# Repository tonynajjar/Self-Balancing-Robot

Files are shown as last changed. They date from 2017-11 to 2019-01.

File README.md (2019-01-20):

# Steady
Self-Balancing Robot: https://www.youtube.com/watch?time_continue=1&v=wG_vcWqeqLw

This project aimed to design, construct and program a self-balancing robot. The following objectives have been set:

* Design and assemble the chassis of the robot
* Mount all the electronic hardware on the chassis and make all the electrical connections
* Develop the software to read from the sensors and to control the actuators
* Implement a PID controller to enable the robot to stay upright
* Implement a PID controller to enable the robot to return to move
* Develop the software for wireless control and camera streaming

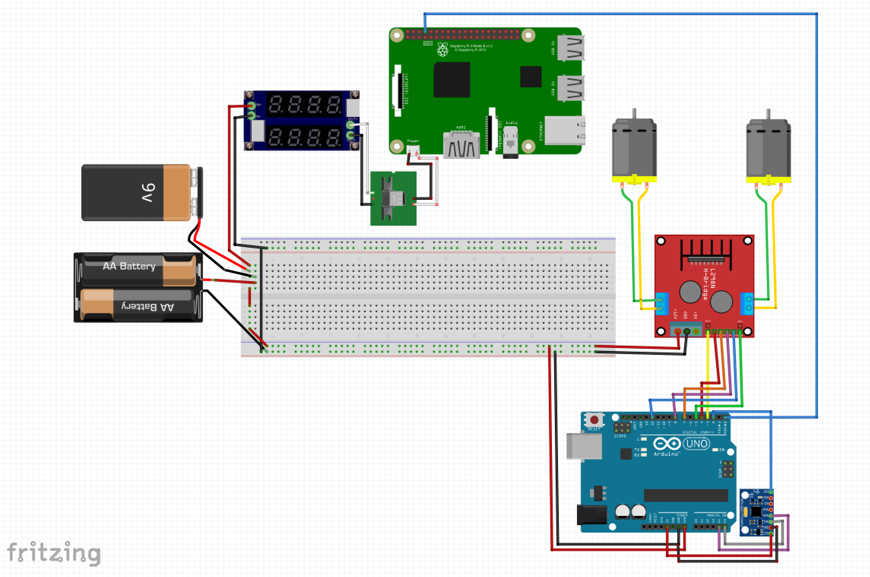
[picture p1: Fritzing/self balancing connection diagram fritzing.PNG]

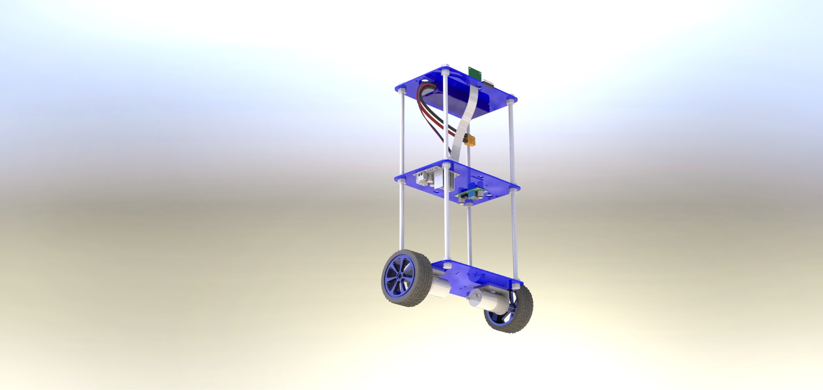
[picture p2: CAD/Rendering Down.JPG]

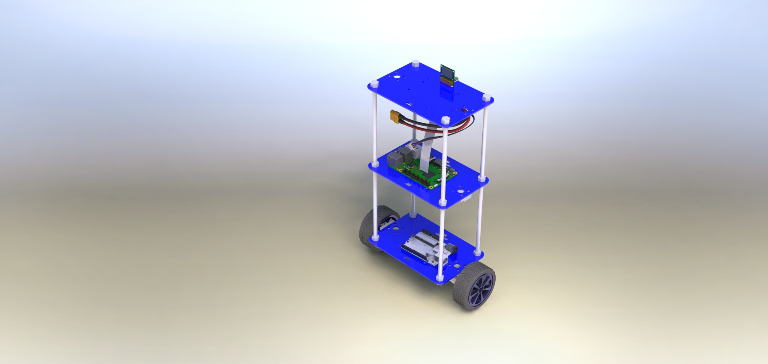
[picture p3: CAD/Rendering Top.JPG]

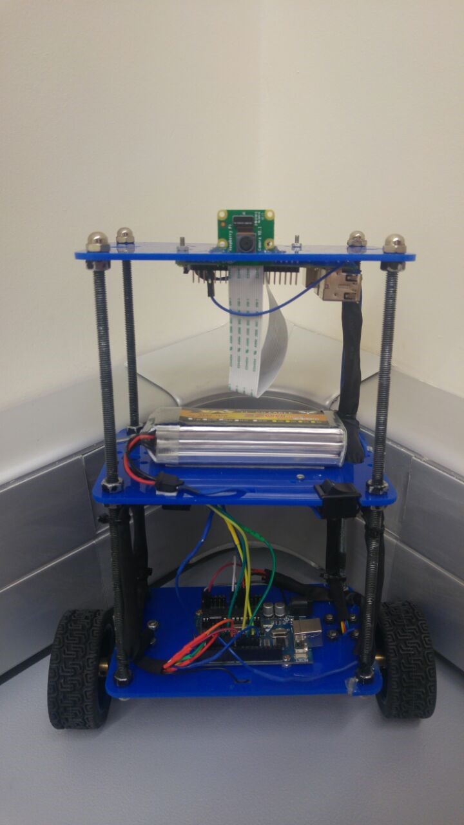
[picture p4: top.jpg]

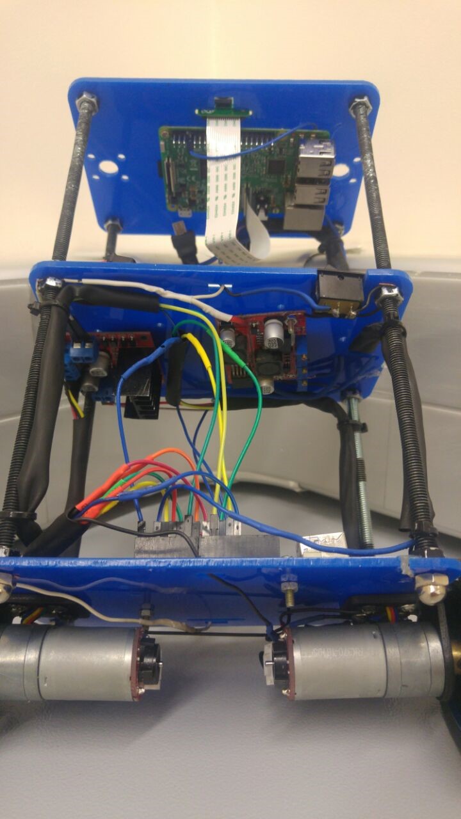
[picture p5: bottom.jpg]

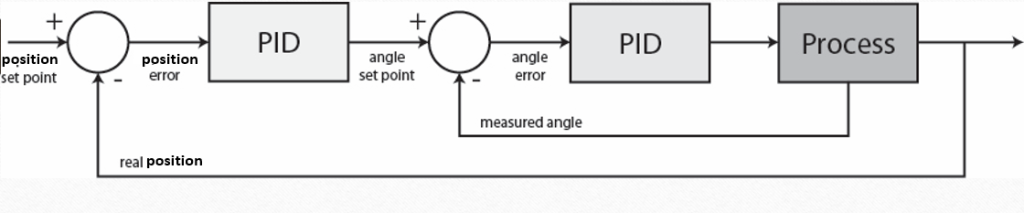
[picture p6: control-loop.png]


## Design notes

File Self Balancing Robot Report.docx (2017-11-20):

Introduction

Self-balancing robots have been a topic of interest of many researchers, students and hobbyists worldwide. In essence, it is an inverted pendulum on wheels, a derivative of the inverted pendulum on a cart. Unlike traditional robots, which are in a constant state of equilibrium, the self-balancing robot is a naturally unstable system; its design is more complex, as it needs to be actively controlled to maintain its upright position. The primary practical application of a self-balancing robot is human transportation, which was popularized by the release of the Segway.

This project aims to design, construct and program a self-balancing robot. To achieve the aims of the project, following objectives have been set:

- Design and assemble the chassis of the robot
- Mount all the electronic hardware on the chassis and make all the electrical connections
- Develop the software to read from the sensors and to control the actuators
- Implement a PID controller to enable the robot to stay upright
- Implement a PID controller to enable the robot to return to its original position if pushed
- Develop the software for wireless control and camera streaming

This report discusses the theoretical considerations made at the start of the project, the steps that were taken to implement the self-balancing code, the analysis of the final results, the interpretation of the final results and finally the recommendations for future continuation of the project

Background research

The inverted pendulum is a classical problem in control systems, and to explore the unstable dynamics, different platforms have been developed. These platforms are similar in many ways, leading to many of the behaviors being comparable. The most common types are the self-balancing robot, Inverted Pendulum on a cart and an inverted pendulum on a linear track, shown in the figure below:

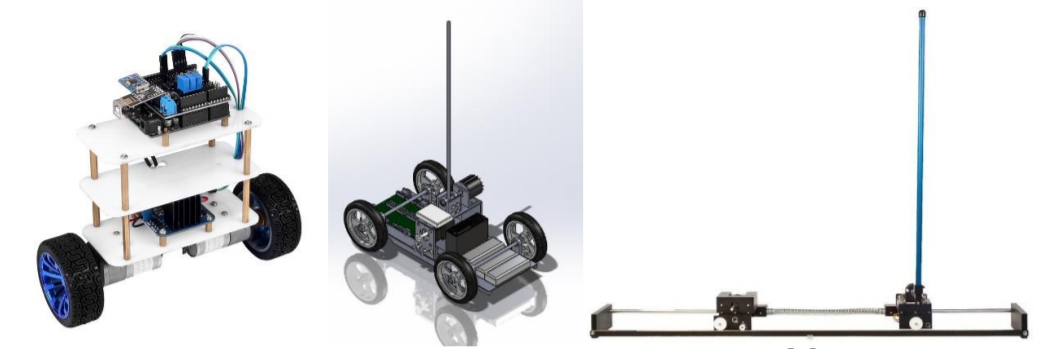
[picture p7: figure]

The Segway is a dynamic system that is commonly referred to as an inverted pendulum.

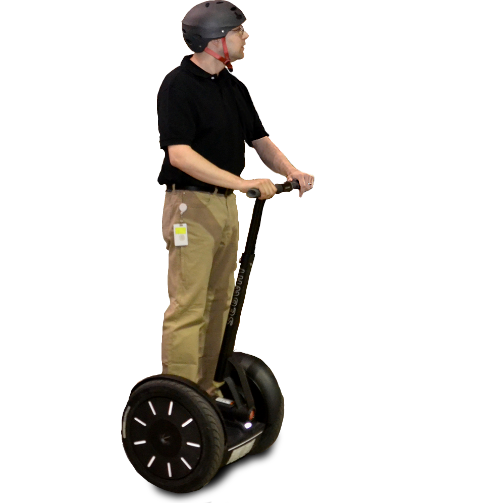
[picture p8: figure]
Image result for segway

To form a two-wheeled inverted pendulum (TWIP), the pendulum is anchored to a base platform that has a wheel mounted on each side. In this case, a motor drives each wheel independently. The torque from the motors makes the base move to balance pitch angle of the pendulum. It can move along curved paths by driving the motors at different speeds. The two-wheeled inverted pendulum has been proposed as a portable transporter due to its high maneuverability

The Segway is a device that transports one person at relatively low speeds. The low-speed (limited to approximately 12 mph) operation combined with its electric propulsion system makes the Segway a candidate for providing short-distance transportation on city streets, sidewalks, and inside buildings. When a Segway is in use, the device is driven by two wheels that are placed side-by-side, rather than the standard in-line configuration of a bicycle or a motorcycle. When the operator leans forward, the wheels turn in unison in the same direction to provide forward motion. In order to stop, the wheels must accelerate forward to get out in front of the system's center of mass and then apply a deceleration torque to slow the system down without causing the operator to fall forward of the device. These operating principles are reversed to allow the system to move backward. In order to turn, the wheels rotate at unequal speeds causing the system to travel in an arc. If the system is not translating forward or backward, then the wheels can rotate in opposite directions to turn the machine in place. Given the side-by-side wheel configuration, and the elevated center of mass, the mechanical design of the transporter is unstable. It will fall over if the computerized control system is not continuously turning the wheels. This constant adjusting of the device is similar to a person balancing an inverted broom in their hand. In order to keep the broom upright, the person must continually move their hand in the direction that the broom is falling. The broom's center of mass to generate a torque that will cause the broom to start rotating in the opposite direction. As a result, the broom is always falling, but the hand motion keeps changing the direction of the fall. Just like the inverted broom, the Segway and rider are always falling. However, it is not possible for the human operator to balance the device, as they can with a human-powered inverted pendulum such as a unicycle. The sensors in the device must constantly be measuring the state of the machine and feeding this information to the computer controller. The controller then uses this feedback signal to adjust the wheel speed so that the forward/backward (pitch) falling motion is maintained within an acceptable envelope so that device and rider do not fall over. Note that under many operating conditions, the system is mechanically stable in the side-to-side (roll) direction. Therefore, the computer does not attempt to control the roll motion. Assuming wheel-ground rolling stiction, the system is also stable in the yaw direction. However, the computer must change the yaw rate in order to turn the machine in 10 response to the operator input. It also limits the turning rate to a maximum value

Technical discussion / simulation study

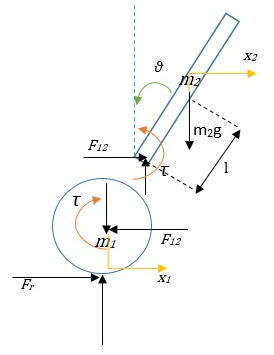
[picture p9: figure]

The control algorithm that is used to maintain the balance on the autonomous self-balancing robot is the PID controller. The proportional, integral, and derivative (PID) controller is well known as a three term controller. The input to the controller is the error from the system. The Kp, Ki, and Kd are referred as the proportional, integral, and derivative constants (the three terms get multiplied by these constants) respectively. In the PID controller the error gets managed in three ways. The error will be used on the PID controller to execute the proportional term, integral term for reduction of steady state errors, and the derivative term to handle overshoots

Results

Conclusion

During the project a robot has been designed and built from scratch. Mechanically it looks and works as planned. A mathematical model of the robot and two control designs were calculated and simulated to verify the systems behavior.

References

Appendix

http://oaktrust.library.tamu.edu/bitstream/handle/1969.1/155306/SUNG-THESIS-2015.pdf?sequence=1

http://publications.lib.chalmers.se/records/fulltext/163397.pdf

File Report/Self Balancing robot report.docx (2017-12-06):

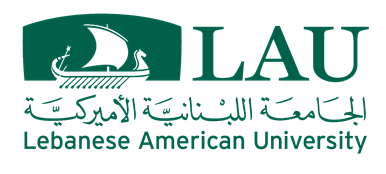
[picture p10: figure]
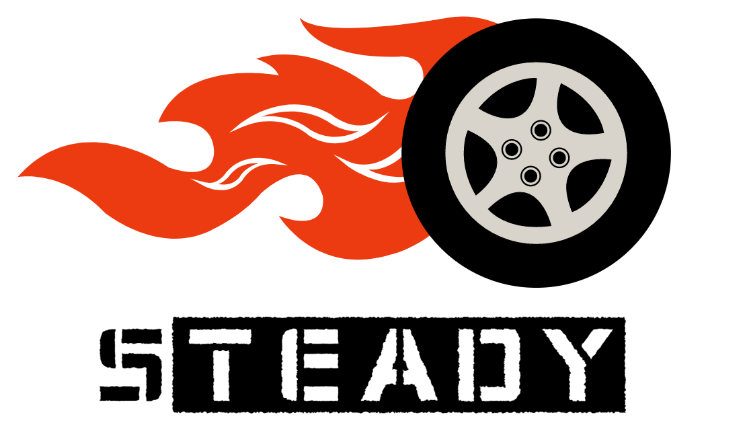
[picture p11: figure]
A picture containing vector graphics Description generated with high confidence

# Self-Balancing

# Robot

Tony Najjar

Walid Aboul hosn

# Introduction

Self-balancing robots have been a topic of interest of many researchers, students and hobbyists worldwide. It is essentially an inverted pendulum on wheels, a derivative of the inverted pendulum on a cart. Unlike traditional robots, which are in a constant state of equilibrium, the self-balancing robot is a naturally unstable system; its design is more complex, as it needs to be actively controlled to maintain its upright position. The primary practical application of a self-balancing robot is human transportation, which was popularized by the release of the Segway.

- This project aims to design, construct and program a self-balancing robot. To achieve the aims of the project, following objectives have been set:
- Design and assemble the chassis of the robot
- Mount all the electronic hardware on the chassis and make all the electrical connections
- Develop the software to read from the sensors and to control the actuators
- Implement a PID controller to enable the robot to stay upright
- Implement a PID controller to enable the robot to return to move
- Develop the software for wireless control and camera streaming

A self-balancing robot has been designed and built from scratch. Mechanically it looks and works as planned. A mathematical model of the robot and a PID control architecture were calculated and simulated to verify the system’s behavior. The PID controllers were successfully implemented on the robot together with a Kalman filter to make it balance, even with disturbances.

# Background Research

The inverted pendulum is a classical problem in control systems, and to explore the unstable dynamics, different platforms have been developed. These platforms are similar in many ways, leading to many of the behaviors being comparable. The most common types are the self-balancing robot, Inverted Pendulum on a cart and an inverted pendulum on a linear track, shown in the figure below:


The most renowned practical application of the inverted pendulum is the Segway, a dynamic system used for individual transportation.

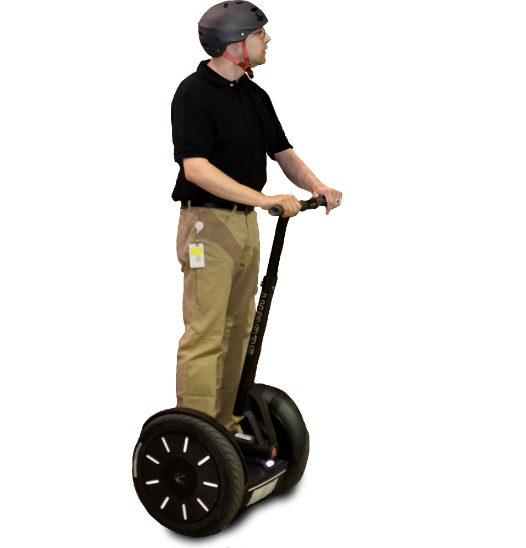
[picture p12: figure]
Image result for segway

The Segway is anchored to a base platform that has a wheel mounted on each side. In this case, a motor drives each wheel independently. The torque from the motors makes the base move to balance pitch angle of the pendulum. It can move along curved paths by driving the motors at different speeds. The two-wheeled inverted pendulum has been proposed as a portable transporter due to its high maneuverability

The Segway is a device that transports one person at relatively low speeds. The low-speed (limited to approximately 12 mph) operation combined with its electric propulsion system makes the Segway a candidate for providing short-distance transportation on city streets, sidewalks, and inside buildings. When a Segway is in use, the device is driven by two wheels that are placed side-by-side, rather than the standard in-line configuration of a bicycle or a motorcycle. When the operator leans forward, the wheels turn in unison in the same direction to provide forward motion. In order to stop, the wheels must accelerate forward to get out in front of the system's center of mass and then apply a deceleration torque to slow the system down without causing the operator to fall forward of the device. These operating principles are reversed to allow the system to move backward. In order to turn, the wheels rotate at unequal speeds causing the system to travel in an arc. If the system is not translating forward or backward, then the wheels can rotate in opposite directions to turn the machine in place. Given the side-by-side wheel configuration, and the elevated center of mass, the mechanical design of the transporter is unstable. It will fall over if the computerized control system is not continuously turning the wheels. This constant adjusting of the device is similar to a person balancing an inverted broom in their hand. In order to keep the broom upright, the person must continually move their hand in the direction that the broom is falling. The broom's center of mass to generate a torque that will cause the broom to start rotating in the opposite direction. As a result, the broom is always falling, but the hand motion keeps changing the direction of the fall. Just like the inverted broom, the Segway and rider are always falling. However, it is not possible for the human operator to balance the device, as they can with a human-powered inverted pendulum such as a unicycle. The sensors in the device must constantly be measuring the state of the machine and feeding this information to the computer controller. The controller then uses this feedback signal to adjust the wheel speed so that the forward/backward (pitch) falling motion is maintained within an acceptable envelope so that device and rider do not fall over. Note that under many operating conditions, the system is mechanically stable in the side-to-side (roll) direction. Therefore, the computer does not attempt to control the roll motion. Assuming wheel-ground rolling stiction, the system is also stable in the yaw direction.

# Technical discussion & Simulation study

## Mathematical Modeling

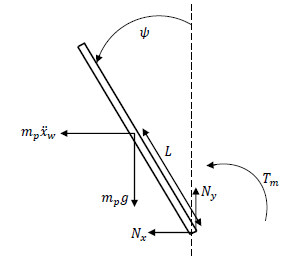
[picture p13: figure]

Pendulum

(1) Tm + mpgLsinψ + mp x wLcosψ = Jpψ
(2) −Nx − mp x w = mp x p
(3) Ny − mpg = mp y p
(4) xp = −Lsinψ
(5) yp = −Lcosψ
(6) x p = −L ψ cosψ + L ψ ² sinψ
(7) y p = −L ψ sinψ + L ψ ² cosψ

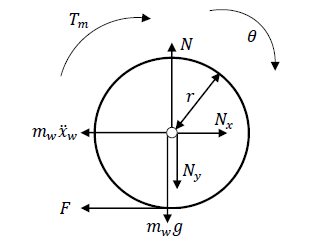
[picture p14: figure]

Wheels

(8) Tm + Fr = Jw θ
(9) Nx − mw x w − F = 0
(10) N − Ny − mwg = mw y w
(11) x w = θ r
(12) y w = 0

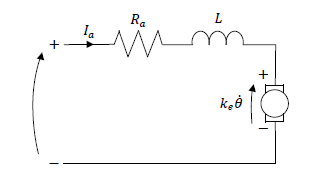
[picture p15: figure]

Motors

(13) U = RaIa + keθ
(14) Tm = nktIa
(15) Ia = U − ke θ Ra
(16) Tm = nktU Ra − nkekt θ Ra

Nonlinear Result

(17) ψ =
(18) ((Jw(gLRampsinψ + 2nkt(U – ke θ)) + r(LrRampsinψ(mp(g – Lψ2cosψ) + gmw)+2nkt(U – keθ)(mp(Lcosψ + r) + rmw))))/((Ra(Jp(Jw + r 2 (mp + mw)) – L2 r2 m2 p cos2ψ)))
(19) θ = Lrmpcosψ (gLRampsinψ + 2nkt (U − ke θ )) + Jp (2nkt (U − ke θ ) − LrRamp ψ ² sinψ (Ra (Jp (Jw + r ² (mp + mw)) − L²r ²m² p cos²ψ))

Linear Result

We can linearize the system by approximating cosθ= 1 and sinθ= θ since θ is considered very small

(20) ψ = ((Jw (gLRampψ +2nkt (U-ke θ))+r(LrRampψ (mp(g - Lψ2)+gmw)+2nkt (U-keθ)(mp (L+r) + rmw))))/((Ra(Jp(Jw + r2 (mp + mw)) - L2r2m2 p)))
(21) θ = Lrmp (gLRampψ + 2nkt (U − ke θ )) + Jp (2nkt (U − ke θ ) − LrRamp ψ ²ψ (Ra (Jp (Jw + r²(mp + mw)) − L²r ²m² p))

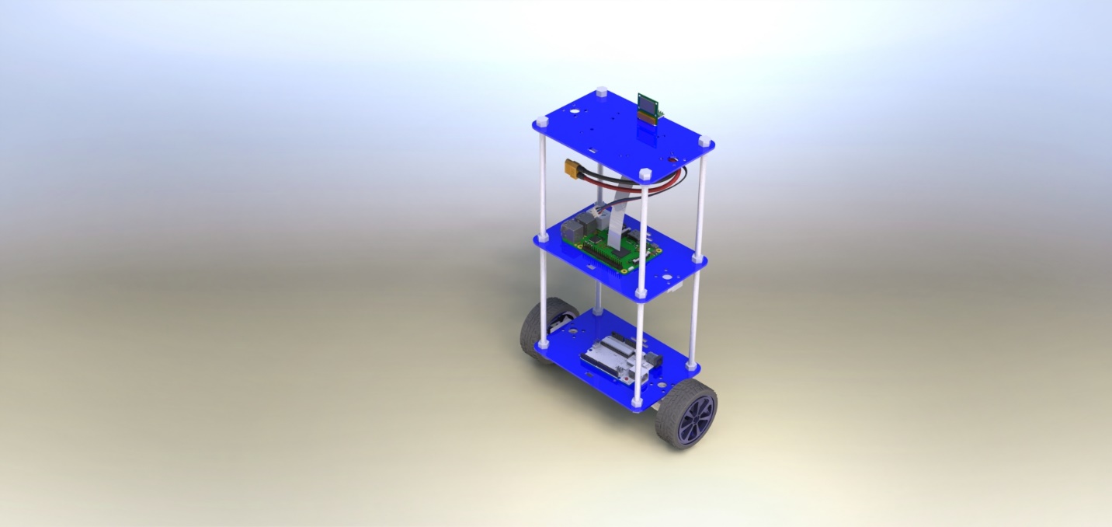
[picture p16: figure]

## CAD Modeling

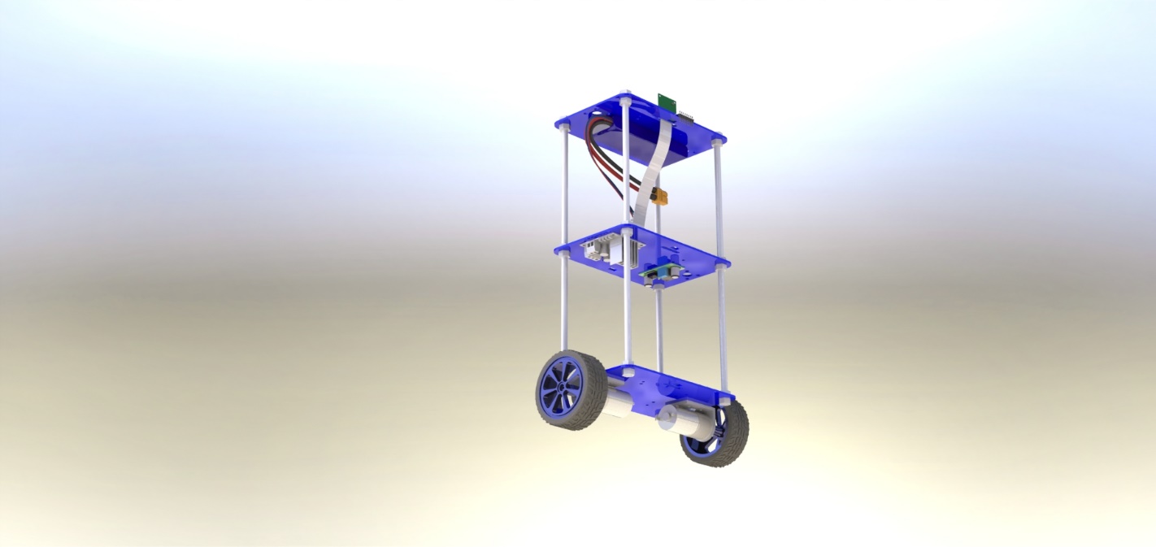
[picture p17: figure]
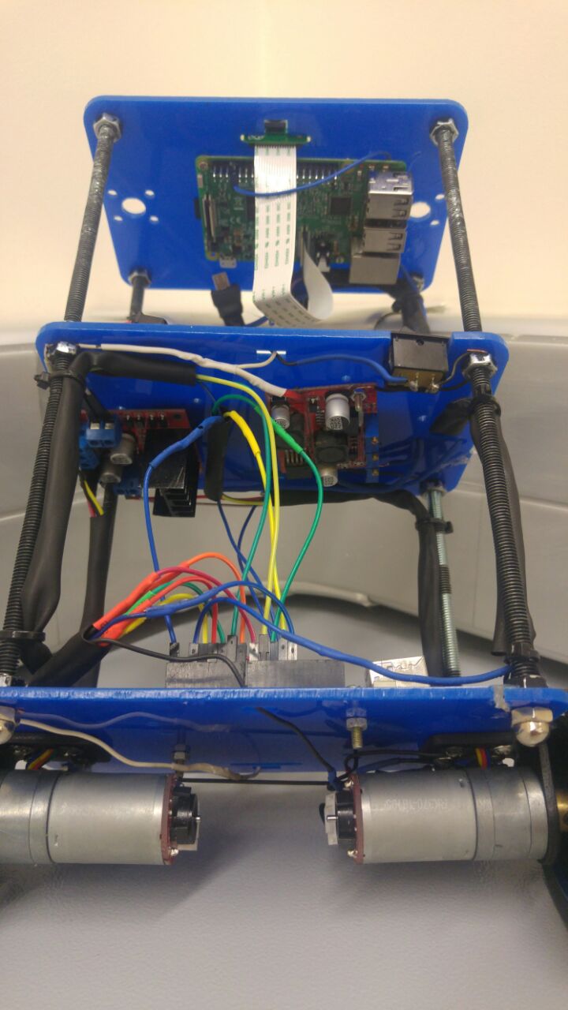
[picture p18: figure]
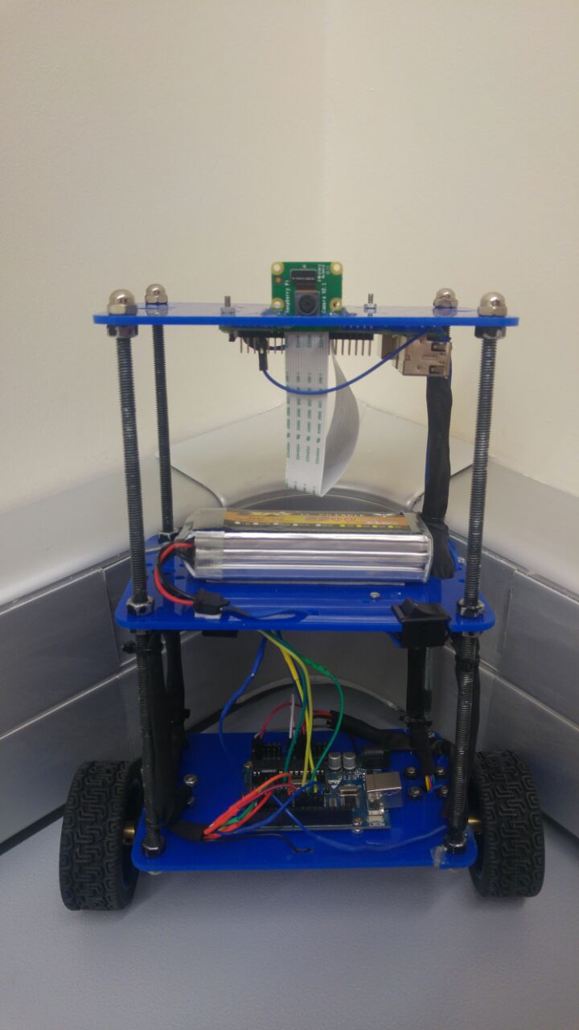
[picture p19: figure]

| Item | Quantity
Mechanical | Threaded Rods | 4
| Plexiglass Board | 3
| Motor Brackets | 2
Electrical | Arduino | 1
| Raspberry Pi | 1
| Raspberry Pi camera | 1
| IMU MPU6050 | 1
| Motor Driver L298N | 1
| Step-down DC Transformer | 1
| Battery | 1
| Geared Motors with Encoders | 2

## Hardware Wiring

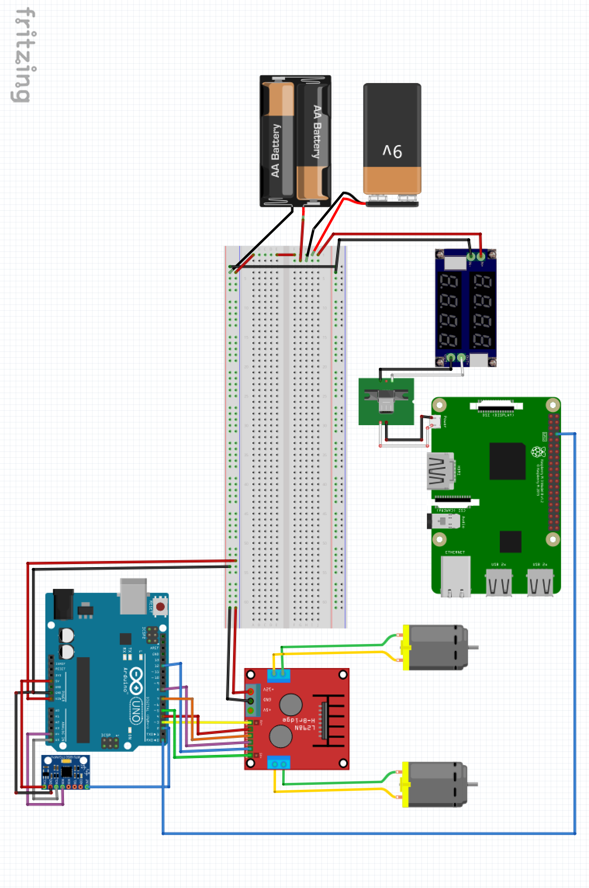
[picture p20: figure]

# Results

## Balancing Control

The control algorithm that is used to maintain the balance on the autonomous self-balancing robot is the PID controller. The proportional, integral, and derivative (PID) controller is well known as a three-term controller. The input to the controller is the error from the system. The Kp, Ki, and Kd are referred as the proportional, integral, and derivative constants (the three terms get multiplied by these constants) respectively. In the PID controller the error gets managed in three ways. The error will be used on the PID controller to execute the proportional term, integral term for reduction of steady state errors, and the derivative term to handle overshoots

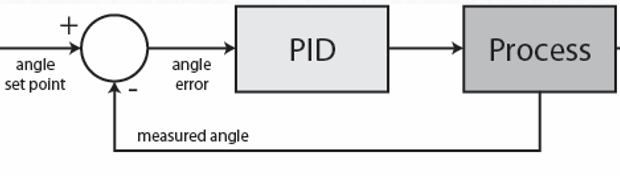
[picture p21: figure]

It is worthwhile mentioning that the LQR controller is also vastly used in inverted pendulum applications. LQR is a form of optimal control that aims to minimize the performance index whist taking into account the control effort, as often, higher input effort would imply higher energy consumption. LQR control requires derivation of the state-space model of the system, thus it is more challenging to implement.

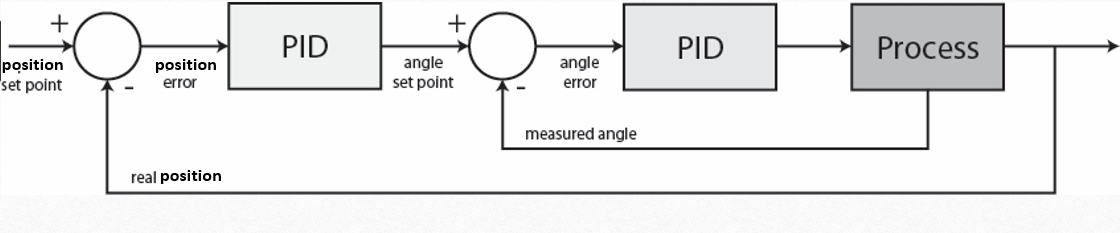
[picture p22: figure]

## Position Control

One issue with the balancing control loop is that the robot has no insight on its position and could stay upright while constantly moving. This is usually undesirable due to space constraints. To solve this issue we used parallel compensation; an extra encoder PID controller was added to the scheme to control the robot’s position. The encoder PID measures the error in position and outputs the setpoint for the angle PID loop which in turn will control the PWM of the motors. So if there's an offset in position the angle setpoint will change to, let say -2 degrees (from upright 0 degrees). So now the angle PID will make the robot move in order to correct the angle offset and therefore also correcting the position error.

## Wireless Control and Camera Streaming

Wireless control and camera streaming was implemented on the robot using a Raspberry Pi.

The small computer receives keyboard commands via Wifi and communicates them serially to the Arduino. The only factor we control is the position setpoint; we set it to be slightly positive or negative to make the robot lean forward or backward and consequently accelerate.

As for the on-board camera, the robot has the ability to wirelessly stream with minimum lag the camera’s output over the network.

# Conclusion

Overall, this self-balancing robot project was a big success, meeting all the objectives set at the beginning. The robot’s performance compares very well with other self-balancing robots found on the internet in terms of smooth balancing and position control.

We look forward to enhancing the robot in many ways such as smoothening the controllers for better transient response and adding: computer vision (to follow a ball for example), ultrasonic sensors for table/stair edge detection and side arms for fall cushioning and automatic stand up.

# References

https://www.coursehero.com/file/p1e3kuv/Other-studies-considered-changing-the-relative-position-of-the-global-center-of/

http://ieeexplore.ieee.org/iel7/6550152/6564841/06565146.pdf

http://www.ijcert.org/V2I1249.pdf

# Appendix

## Arduino

#include <PID_v1.h>

#include <LMotorController.h>

#include "I2Cdev.h"

#include <SoftwareSerial.h>

#include <Encoder.h>

#include "MPU6050_6Axis_MotionApps20.h"

#if I2CDEV_IMPLEMENTATION == I2CDEV_ARDUINO_WIRE

#include "Wire.h"

#endif

#define MOVE_BACK_FORTH 0

#define MIN_ABS_SPEED 80

Encoder left(9, 6);

Encoder right(10, 11);

long oldPosition = -999;

int encCount = 0;

//MPU

unsigned long counter;

MPU6050 mpu;

// MPU control/status vars

bool dmpReady = false; // set true if DMP init was successful

uint8_t mpuIntStatus; // holds actual interrupt status byte from MPU

uint8_t devStatus; // return status after each device operation (0 = success, !0 = error)

uint16_t packetSize; // expected DMP packet size (default is 42 bytes)

uint16_t fifoCount; // count of all bytes currently in FIFO

uint8_t fifoBuffer[64]; // FIFO storage buffer

// orientation/motion vars

Quaternion q; // [w, x, y, z] quaternion container

VectorFloat gravity; // [x, y, z] gravity vector

float ypr[3]; // [yaw, pitch, roll] yaw/pitch/roll container and gravity vector

//PID

double originalSetpoint = 174.29;

double setpoint = originalSetpoint;

double movingAngleOffset = 1.5;

double input = originalSetpoint, output;

int moveState = 0; //0 = balance; 1 = back; 2 = forth

double posInput, posOutput, posSetpoint = 0;

PID pid(&input, &output, &setpoint, 25, 240, 2, DIRECT);

PID posPID(&posInput, &posOutput, &posSetpoint, 0.8, 0, 1, REVERSE);

//MOTOR CONTROLLER

int motorSpeed;

double motorSpeedFactorLeft = 0.8;

double motorSpeedFactorRight = 1;

//MOTOR CONTROLLER

const int ENA = 3;

const int IN1 = 4;

const int IN2 = 7;

const int IN3 = 8;

const int IN4 = 12;

const int ENB = 5;

LMotorController motorController(ENA, IN1, IN2, ENB, IN3, IN4, motorSpeedFactorLeft, motorSpeedFactorRight);

//timers

long time5Hz = 0;

volatile bool mpuInterrupt = false; // indicates whether MPU interrupt pin has gone high

void dmpDataReady()

{

mpuInterrupt = true;

}

void setup()

{

// join I2C bus (I2Cdev library doesn't do this automatically)

#if I2CDEV_IMPLEMENTATION == I2CDEV_ARDUINO_WIRE

Wire.begin();

TWBR = 24; // 400kHz I2C clock (200kHz if CPU is 8MHz)

#elif I2CDEV_IMPLEMENTATION == I2CDEV_BUILTIN_FASTWIRE

Fastwire::setup(400, true);

#endif

Serial.begin(115200);

while (!Serial); // wait for Leonardo enumeration, others continue immediately

// initialize device

Serial.println(F("Initializing I2C devices..."));

mpu.initialize();

// verify connection

Serial.println(F("Testing device connections..."));

Serial.println(mpu.testConnection() ? F("MPU6050 connection successful") : F("MPU6050 connection failed"));

// load and configure the DMP

Serial.println(F("Initializing DMP..."));

devStatus = mpu.dmpInitialize();

// supply your own gyro offsets here, scaled for min sensitivity

mpu.setXGyroOffset(220);

mpu.setYGyroOffset(76);

mpu.setZGyroOffset(-85);

mpu.setZAccelOffset(1788); // 1688 factory default for my test chip

// make sure it worked (returns 0 if so)

if (devStatus == 0)

{

// turn on the DMP, now that it's ready

Serial.println(F("Enabling DMP..."));

mpu.setDMPEnabled(true);

// enable Arduino interrupt detection

Serial.println(F("Enabling interrupt detection (Arduino external interrupt 0)..."));

attachInterrupt(0, dmpDataReady, RISING);

mpuIntStatus = mpu.getIntStatus();

Serial.println(F("DMP ready! Waiting for first interrupt..."));

dmpReady = true;

// get expected DMP packet size for later comparison

packetSize = mpu.dmpGetFIFOPacketSize();

//setup PID

pid.SetMode(AUTOMATIC);

pid.SetSampleTime(100);

pid.SetOutputLimits(-255, 255);

posPID.SetMode(AUTOMATIC);

posPID.SetSampleTime(100);

posPID.SetOutputLimits(-movingAngleOffset, movingAngleOffset);

}

else{

Serial.print(F("DMP Initialization failed (code "));

Serial.print(devStatus);

Serial.println(F(")"));

}

}

void loop()

{

// if programming failed, don't try to do anything

if (!dmpReady) {

return;

}

// wait for MPU interrupt or extra packet(s) available

while (!mpuInterrupt && fifoCount < packetSize){

//Serial.println(abs(input - originalSetpoint));

if (abs(input - originalSetpoint) > 20) {

motorController.move(0);

break;

}

double newPosition = (right.read() + left.read()) / 2;

if (newPosition != oldPosition && abs(newPosition - oldPosition) > 5) {

oldPosition = newPosition;

posInput = newPosition / 100;

//Serial.println(posInput);

}

// Serial.println(posInput);

//no mpu data - performing PID calculations and output to motors

posPID.Compute();

calculateSetpoint();

pid.Compute();

if (input > setpoint + 0.3 || input < setpoint - 0.3) {

motorController.move(output, MIN_ABS_SPEED);

}

else {

motorController.move(0);

}

unsigned long currentMillis = millis();

if (currentMillis - time5Hz >= 5000)

{

//moveBackForth();

time5Hz = currentMillis;

}

}

// reset interrupt flag and get INT_STATUS byte

mpuInterrupt = false;

mpuIntStatus = mpu.getIntStatus();

// get current FIFO count

fifoCount = mpu.getFIFOCount();

// check for overflow (this should never happen unless our code is too inefficient)

if ((mpuIntStatus & 0x11) || fifoCount == 1024)

{

// reset so we can continue cleanly

mpu.resetFIFO();

Serial.println(F("FIFO overflow!"));

// otherwise, check for DMP data ready interrupt (this should happen frequently)

}

else if (mpuIntStatus & 0x02)

{

// wait for correct available data length, should be a VERY short wait

while (fifoCount < packetSize) fifoCount = mpu.getFIFOCount();

// read a packet from FIFO

mpu.getFIFOBytes(fifoBuffer, packetSize);

// track FIFO count here in case there is > 1 packet available

// (this lets us immediately read more without waiting for an interrupt)

fifoCount -= packetSize;

mpu.dmpGetQuaternion(&q, fifoBuffer);

mpu.dmpGetGravity(&gravity, &q);

mpu.dmpGetYawPitchRoll(ypr, &q, &gravity);

input = ypr[2] * 180 / M_PI + 180;

}

}

void calculateSetpoint() {

if (Serial.available()) {

counter = millis();

char c = Serial.read();

//Serial.println(c);

switch (c) {

case 'w':

motorController.setMotorConst(1, 1);

setpoint = originalSetpoint + movingAngleOffset;

break;

case 's':

motorController.setMotorConst(1, 1);

setpoint = originalSetpoint - movingAngleOffset;

break;

case 'a':

motorController.setMotorConst(0.5, 1);

setpoint = originalSetpoint + movingAngleOffset;

break;

case 'd':

motorController.setMotorConst(1, 0.5);

setpoint = originalSetpoint + movingAngleOffset;

break;

}

}

else if (millis() - counter > 500) {

posInput=0;

left.write(0);

right.write(0);

posPID.Compute();

setpoint = originalSetpoint + posOutput;

motorController.setMotorConst(0.75, 1);

}

}

## Raspberry Pi

import sys, tty, termios

import serial

ser = serial.Serial(port='/dev/serial0', baudrate=115200,

parity=serial.PARITY_NONE,

stopbits=serial.STOPBITS_ONE,

bytesize=serial.EIGHTBITS,

timeout=1)

def getch():

fd = sys.stdin.fileno()

old_settings = termios.tcgetattr(fd)

try:

tty.setraw(sys.stdin.fileno())

ch = sys.stdin.read(1)

finally:

termios.tcsetattr(fd, termios.TCSADRAIN, old_settings)

return ch

while True:

char = getch()

print char

if char == 'p':

break

ser.write(char)

## MATLAB

%Uncomment one set of PID tunings at a time and run the code

clear

M = 0.5;

m = 0.2;

b = 0.1;

I = 0.006;

g = 9.8;

l = 0.3;

q = (M+m)*(I+m*l^2)-(m*l)^2;

s = tf('s');

P_pend = (m*l*s/q)/(s^3 + (b*(I + m*l^2))*s^2/q - ((M + m)*m*g*l)*s/q - b*m*g*l/q);

%Unstable

% Kp = 10;

% Ki = 0;

% Kd = 0;

%Underdamped

Kp = 100;

Ki = 1;

Kd = 1;

%Overdamped

% Kp = 100;

% Ki = 1;

% Kd = 20;

%axis([0, 2.5, -0.2, 0.2]);

C = pid(Kp,Ki,Kd);

T = feedback(series(P_pend,C),1);

t=0:0.01:10;

[Y, T]=impulse(T,t);

h=figure;

subplot(2,1,1)

plot(T,Y)

subplot(2,1,2)

axis([-1 1 0 1.5])

for i=1:1:size(Y)

if ~ishghandle(h)

break

end

x= cosd(Y(i,1));

y= sind(Y(i,1));

link=line([0 y], [0 x], 'LineWidth' , 4);

pause(0.01);

delete(link)

end

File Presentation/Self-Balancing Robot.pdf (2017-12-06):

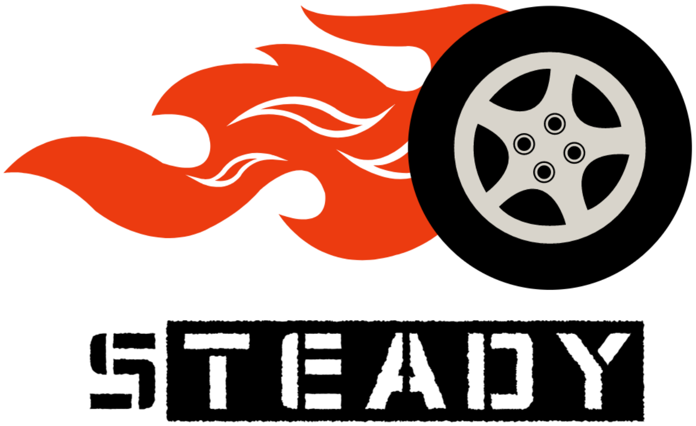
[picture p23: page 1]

# Outline

- Introduction
- Goals
- Background Research
- Working Principle
- Technical Discussion
- CAD
- Wiring and Powering
- Modeling & Simulation
- Control System
- Kalman Filter
- Future Enhancements

# Introduction

A self-balancing robot is essentially an inverted pendulum on wheels

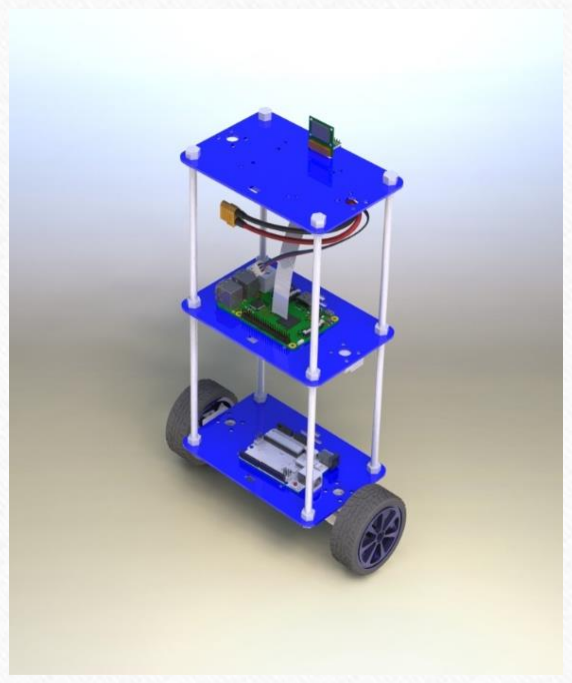
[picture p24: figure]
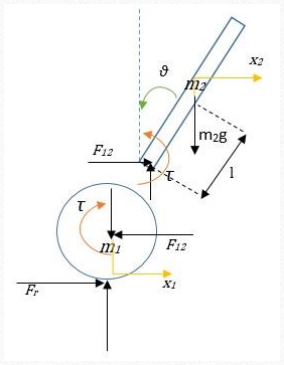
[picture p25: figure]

# Goals

To design, construct and program a self-balancing robot, the following objectives have been set:

- Design and assemble the chassis of the robot
- Mount all the electronic hardware on the chassis and make all the electrical connections
- Develop the software to read from the sensors and to control the actuators
- Implement a PID controller to enable the robot to stay upright
- Add a cascaded PID controller to control robot’s position
- Develop the software for wireless control and camera streaming

# Background Research

The most common types of inverted pendulums are the self-balancing robot, inverted pendulum on a cart and an inverted pendulum on a linear track

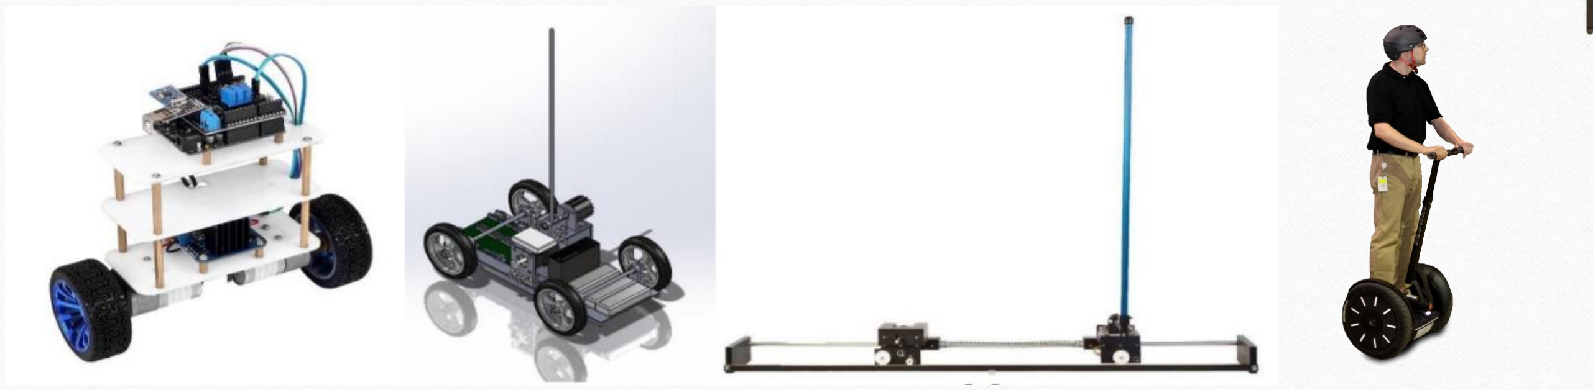
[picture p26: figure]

# Working Principle

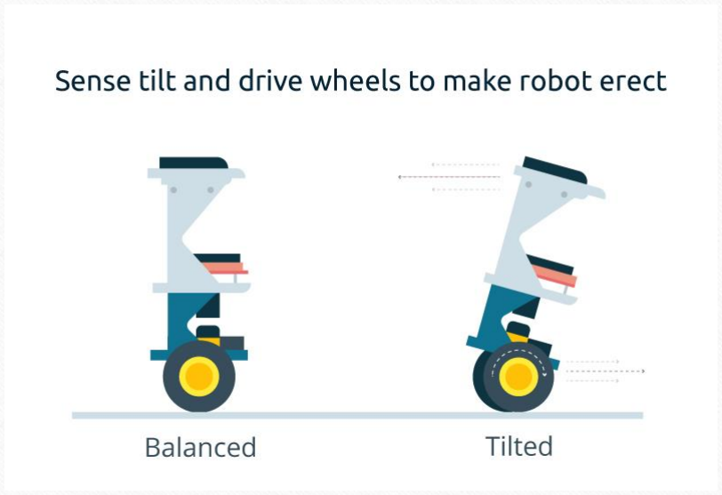
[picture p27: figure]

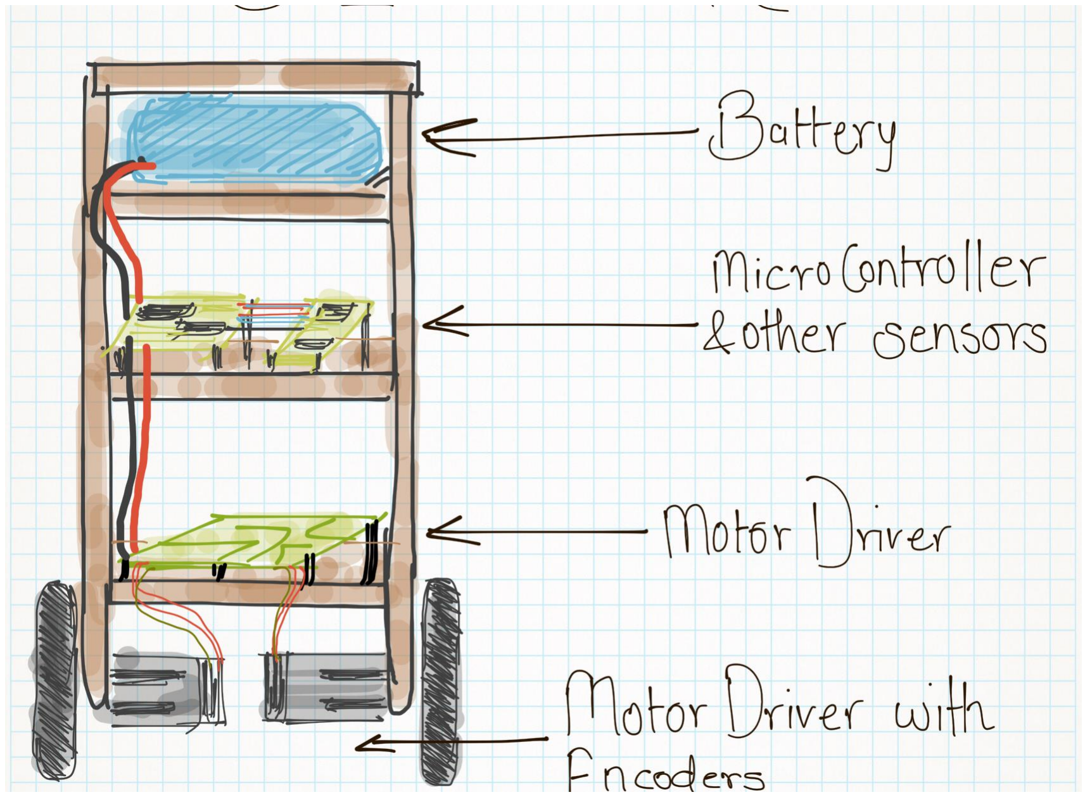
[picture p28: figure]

## CAD & Manufacturing

- Arduino
- Raspberry Pi + Camera
- MPU6050
- Motor Driver
- Step-down DC Transformer
- Battery
- Geared motors with
encoders

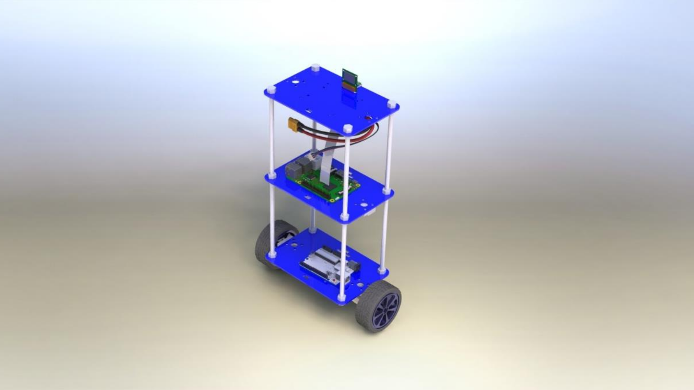
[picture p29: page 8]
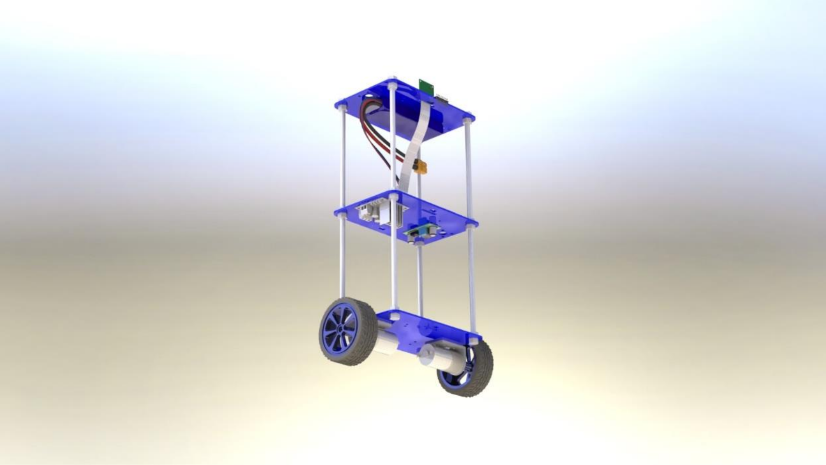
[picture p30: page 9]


## Powering & Wiring

- Main power supply: 12V
- DC transformer for
Raspberry Pi (5V)
- Arduino regulator output for MPU6050 (3.3V)

# Modeling


# Control System

position

From IMU | From Encoders

# Simulation


Unstable | Underdamped | Critically Damped

# Kalman Filter


Out of the scope of this
presentation but here’s a
quick explanation

# Future Enhancements

- Smoothening the controllers for better transient response
- Adding: computer vision (to follow a ball for example)
- Adding ultrasonic sensors for table/stair edge detection
- Adding side arms for fall cushioning and automatic stand up.

# Results

# Time for the Demo!


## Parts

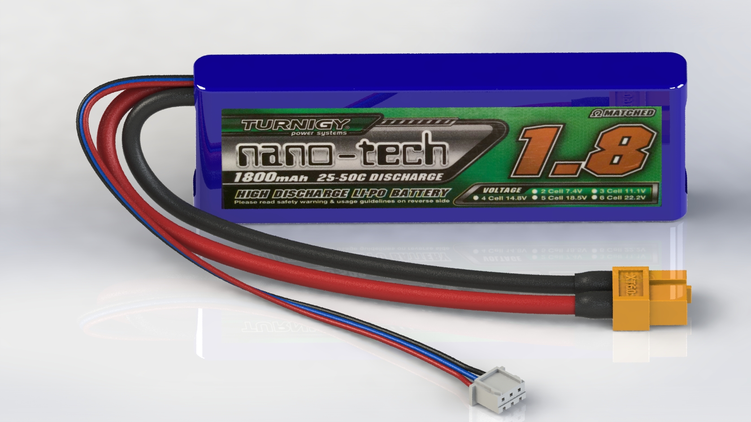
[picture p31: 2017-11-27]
CAD/Parts/battery/Renderings/RENDU - turnigy nanotech 1800mAh 2S (2).JPG

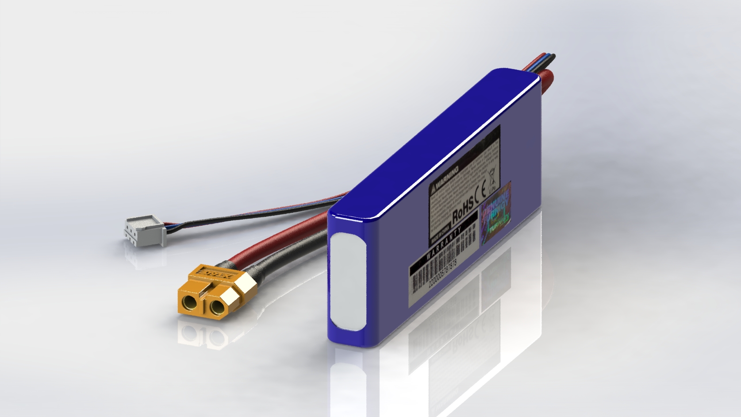
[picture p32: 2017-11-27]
CAD/Parts/battery/Renderings/BACK - Batterie Turnigy Nanotech 1800mAh 2S.JPG

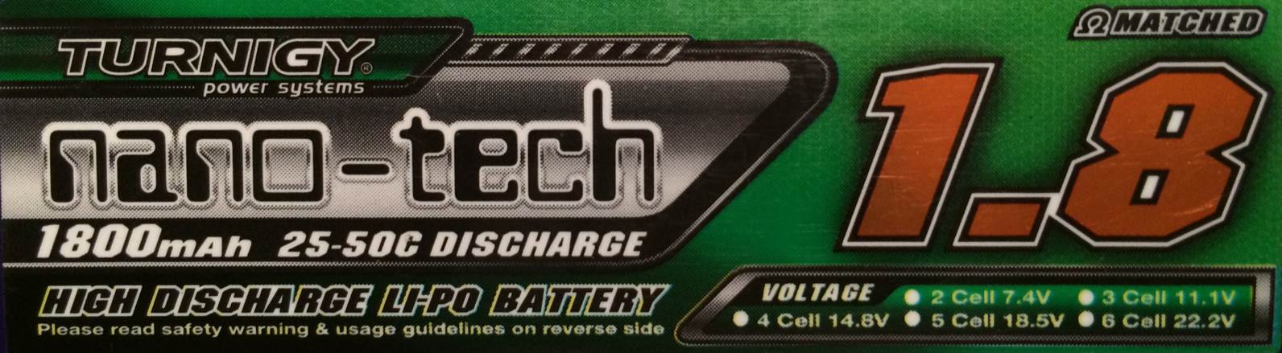
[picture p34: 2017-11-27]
CAD/Parts/battery/Labels/Turnigy_nano-tech-1800mah-25c-battery.JPG

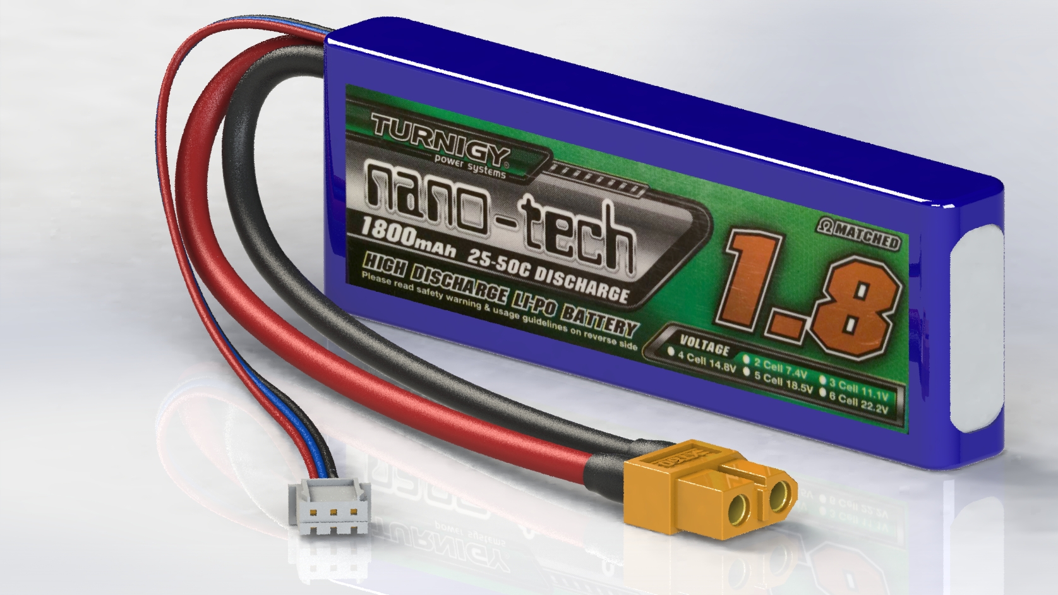
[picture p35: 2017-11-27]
CAD/Parts/battery/Renderings/RENDU - turnigy nanotech 1800mAh 2S.JPG

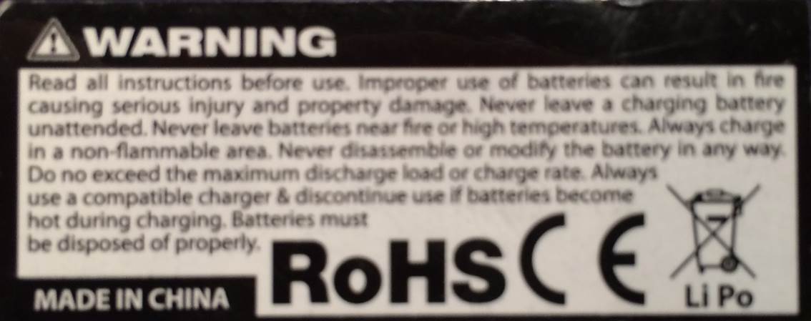
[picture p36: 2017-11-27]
CAD/Parts/battery/Labels/Warning.jpg

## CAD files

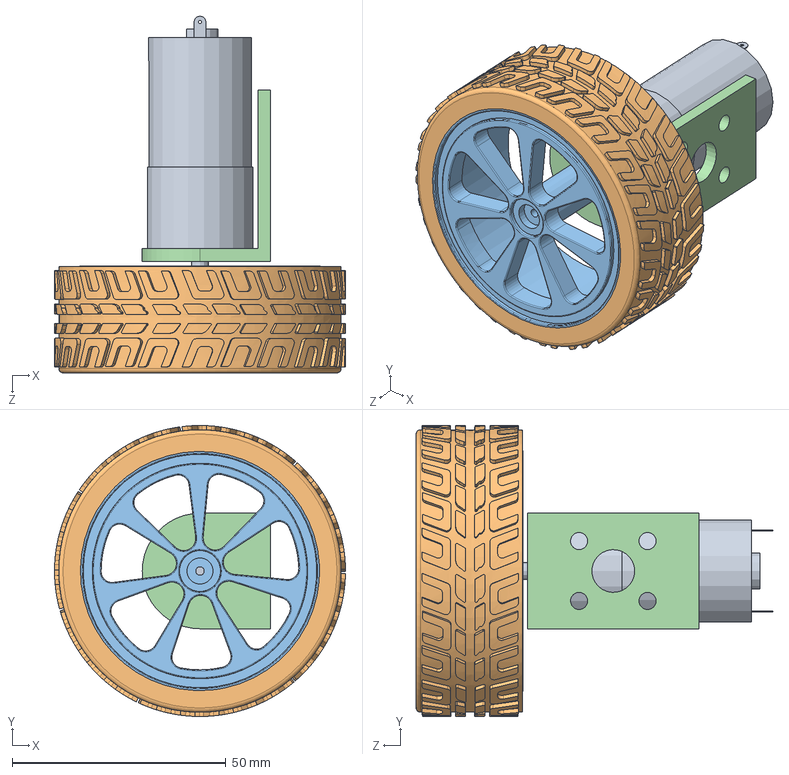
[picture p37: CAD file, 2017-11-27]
CAD/Parts/Robot wheel with motor and bracket/Assem2.SLDASM
68.0 x 68.0 x 83.4 mm
1000rpm_12v_25mm_ebay_motor
Tire
WheelFrame
MotorBracket

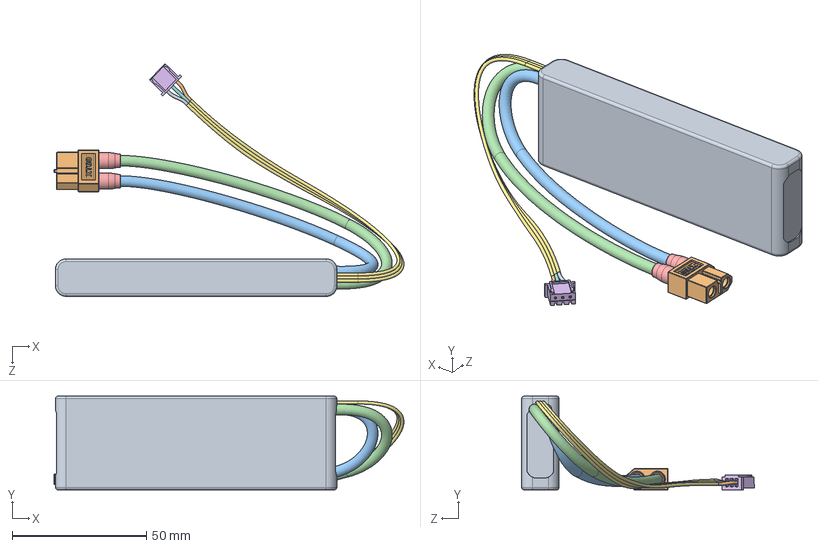
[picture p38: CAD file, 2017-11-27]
CAD/Parts/battery/Turnigy - Batterie Nanotech 1800mAh 2S.SLDASM
130.5 x 35.0 x 86.8 mm
SA_Turnigy_1800mAh_2S__nano_tech_Lipo_Battery
XT60 MALE
Cble^Cable_3-SA_TURNIGY NANOTECH 1800mAh 2S
Cble^Cable_4-SA_TURNIGY NANOTECH 1800mAh 2S
Pièce2^Turnigy - Batterie Nanotech 1800mAh 2S x 2
JST 2S
Pièce7^Turnigy - Batterie Nanotech 1800mAh 2S
Cble^Cable_6-SA_TURNIGY NANOTECH 1800mAh 2S
Cble^Cable_7-SA_TURNIGY NANOTECH 1800mAh 2S-001
Cble^Cable_9-SA_TURNIGY NANOTECH 1800mAh 2S

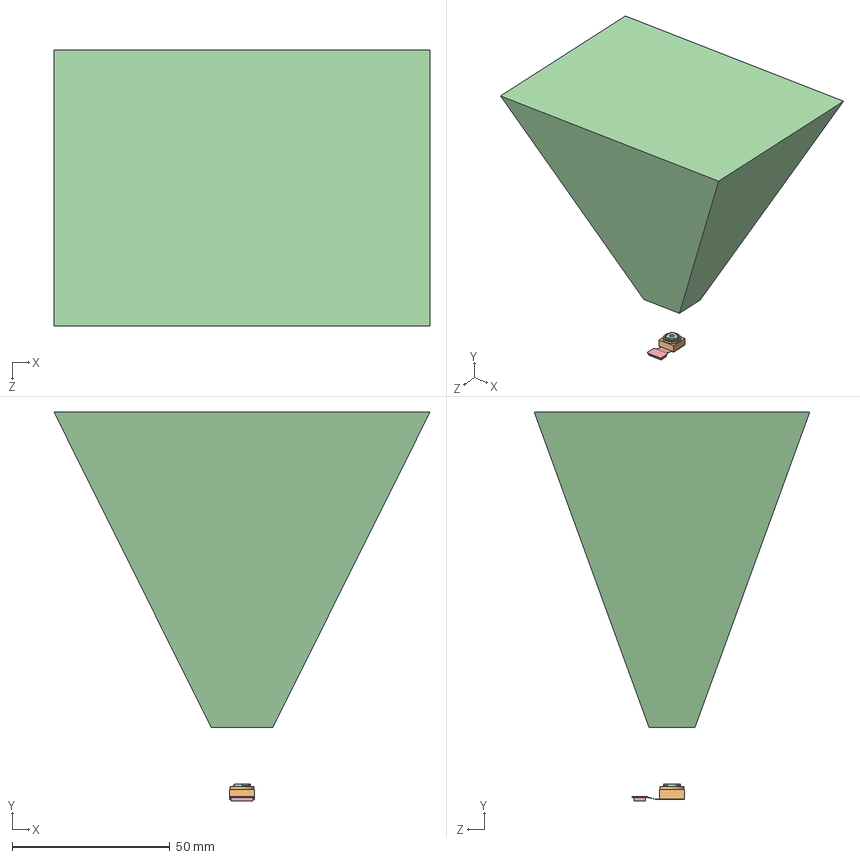
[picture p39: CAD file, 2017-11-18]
CAD/Parts/raspberry-pi-camera-1.snapshot.18/OVA5647.SLDASM
119.2 x 123.2 x 87.4 mm
OVA5647
OVA5647_Housing
OVA5647_IR-Glas
OVA5647_Lens
OVA5647_Pigtail

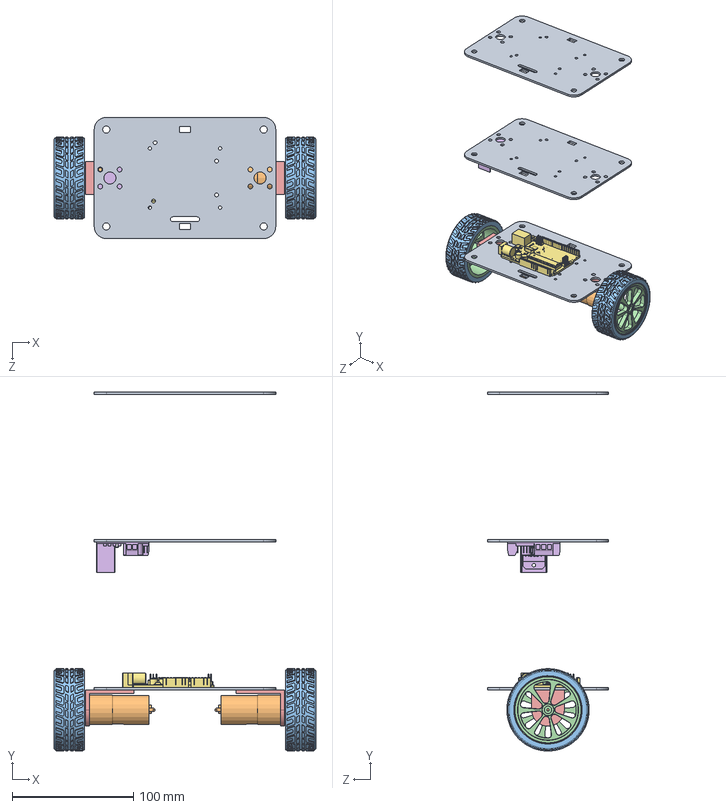
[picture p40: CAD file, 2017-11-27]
CAD/Parts/Robot wheel with motor and bracket/Assem1.SLDASM
216.2 x 296.5 x 100.0 mm
plexichassis x 3
1000rpm_12v_25mm_ebay_motor x 2
Tire x 2
WheelFrame x 2
MotorBracket x 2
L298N
Arduino

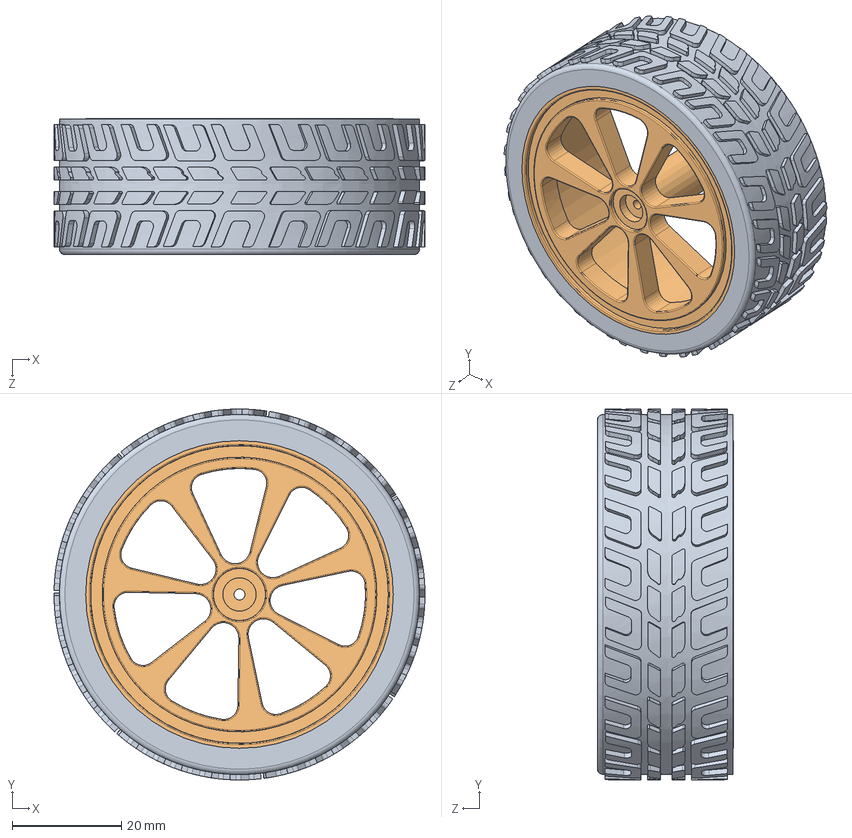
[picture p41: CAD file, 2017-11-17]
CAD/Parts/Robot wheel with motor and bracket/Wheel Assemble.SLDASM
68.0 x 68.0 x 25.0 mm
Tire
WheelFrame

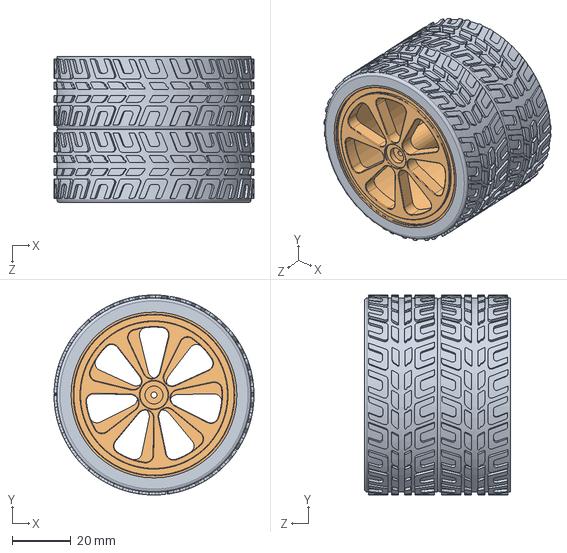
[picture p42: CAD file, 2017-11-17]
CAD/Parts/Robot wheel with motor and bracket/Wheel Assemble simmetry.SLDASM
68.0 x 68.0 x 49.8 mm
WheelFrame
Tire

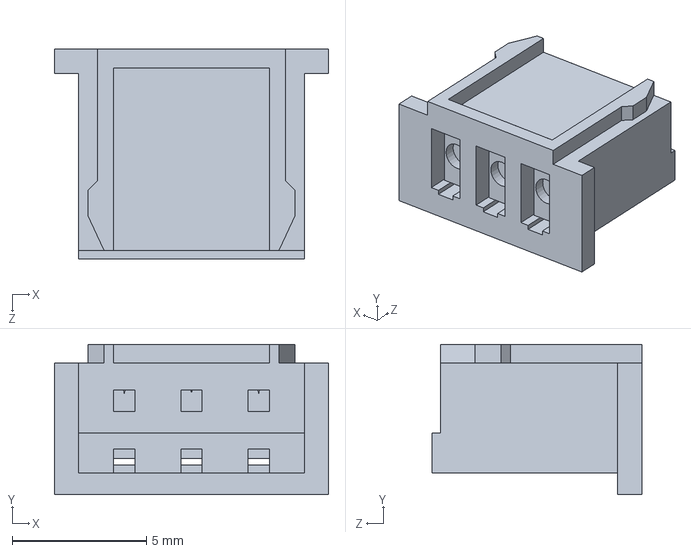
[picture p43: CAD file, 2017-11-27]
CAD/Parts/battery/Composants/JST 2S.SLDPRT
10.2 x 5.60 x 7.80 mm

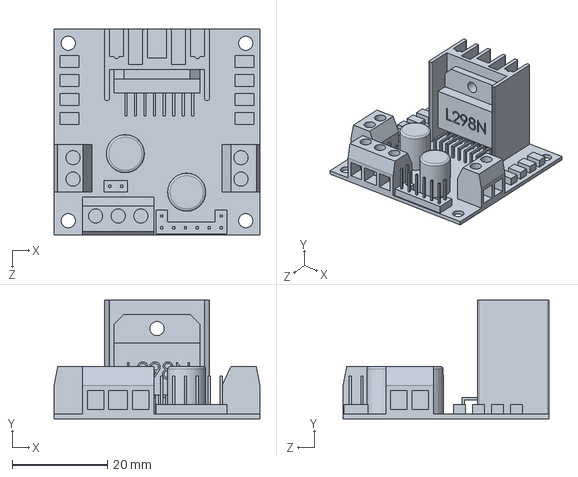
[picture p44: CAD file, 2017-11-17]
CAD/Parts/L298N/L298N.SLDPRT
43.3 x 25.0 x 43.3 mm

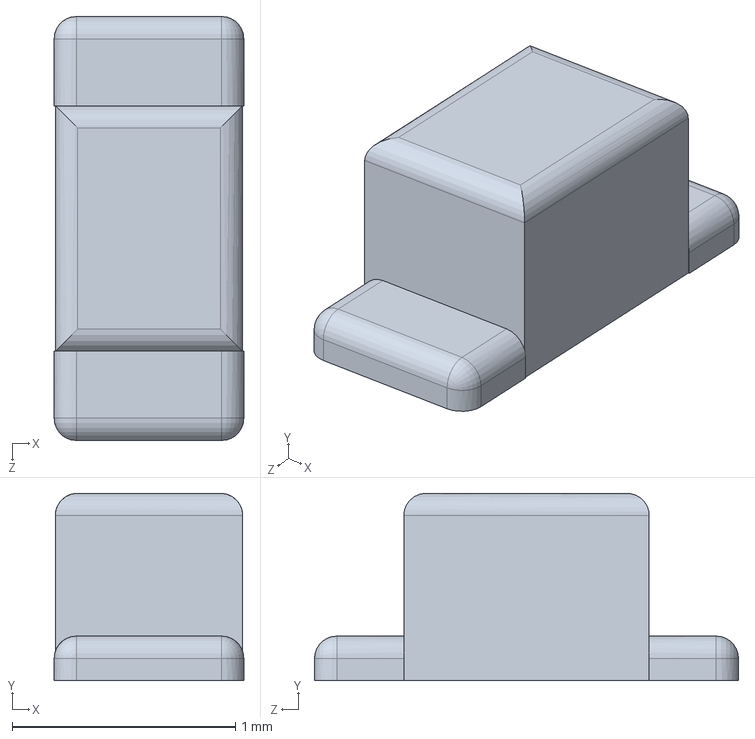
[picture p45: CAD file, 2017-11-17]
CAD/Parts/MPU 6050/Small LED.SLDPRT
0.85 x 0.84 x 1.90 mm

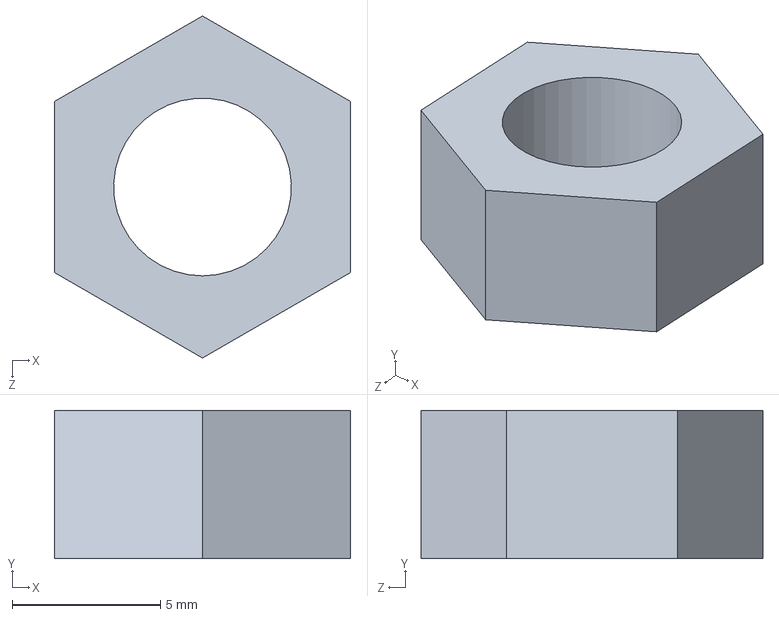
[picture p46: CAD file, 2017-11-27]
CAD/Parts/New folder/Part3.SLDPRT
10.0 x 5.00 x 11.5 mm

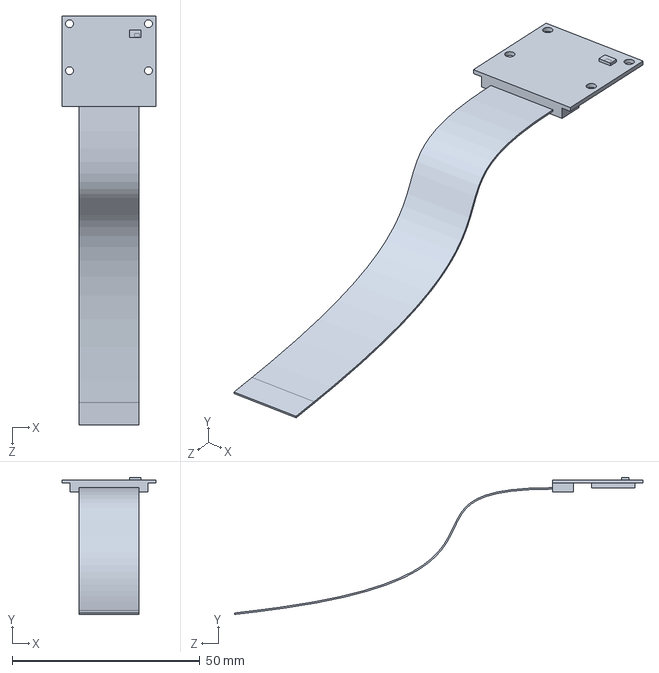
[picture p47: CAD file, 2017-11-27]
CAD/Parts/raspberry-pi-camera-1.snapshot.18/RasPi_Camera_Board.SLDPRT
25.0 x 36.5 x 108.8 mm

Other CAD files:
CAD/Parts/battery/Câbles/Cable_7-SA_TURNIGY NANOTECH 1800mAh 2S-001.sldasm
CAD/Parts/battery/Composants/Electrical_8-SA_TURNIGY NANOTECH 1800mAh 2S.sldasm
CAD/Parts/battery/Câbles/Cable_6-SA_TURNIGY NANOTECH 1800mAh 2S.sldasm
CAD/Parts/battery/Câbles/Cable_4-SA_TURNIGY NANOTECH 1800mAh 2S.sldasm
CAD/Parts/battery/Câbles/Cable_3-SA_TURNIGY NANOTECH 1800mAh 2S.sldasm
CAD/Parts/battery/Câbles/Cable_9-SA_TURNIGY NANOTECH 1800mAh 2S.sldasm
CAD/Parts/battery/3D VIEW - Turnigy Batterie Nanotech 1800mAh 2S.IGS
CAD/Parts/Arduino.SLDPRT
CAD/Parts/CAMERA PI COM LENTE.SLDPRT
CAD/Parts/MPU 6050/Base.SLDPRT
CAD/Parts/MPU 6050/MPU 6050 IMU.SLDASM
CAD/Parts/MPU 6050/MPU 6050 IMU.STEP
CAD/Parts/MPU 6050/Resistor black.SLDPRT
CAD/Parts/MPU 6050/Resistor small black.SLDPRT
CAD/Parts/MPU 6050/Resistor small.SLDPRT
CAD/Parts/MPU 6050/S2NH chip.SLDPRT
CAD/Parts/MPU 6050/pin header.SLDPRT
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

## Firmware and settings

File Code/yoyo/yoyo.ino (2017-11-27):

#include <Wire.h>
#include <PID_v1.h>
#include <Encoder.h>
#include "Kalman.h"
#include <LMotorController.h>
#define RESTRICT_PITCH // Comment out to restrict roll to ±90deg instead
Kalman kalmanX; // Create the Kalman instances
Kalman kalmanY;

double accX, accY, accZ;
double gyroX, gyroY, gyroZ;

double gyroXangle, gyroYangle; // Angle calculate using the gyro only
double compAngleX, compAngleY; // Calculated angle using a complementary filter
double kalAngleX, kalAngleY; // Calculated angle using a Kalman filter

uint32_t timer;
uint8_t i2cData[14]; // Buffer for I2C data
unsigned long counter;


//Define Variables we'll be connecting to
double speedSetpoint = 0; // in a perfect world, 0 would be straight up and down
double speedInput;
double speedOutput;

double angleSetpoint = 0;
double angleInput;
double angleOutput;

const int AVERAGE_COUNT = 20;
float speed_values[AVERAGE_COUNT];
int filter_pos = 0;


//Specify the links and initial tuning parameters
PID speedPID(&speedInput, &speedOutput, &speedSetpoint, 0, 0, 0, DIRECT);
PID anglePID(&angleInput, &angleOutput, &angleSetpoint, 0, 0, 0, REVERSE);



double motorSpeedFactorLeft = 1;
double motorSpeedFactorRight = 1;
//MOTOR CONTROLLER
const int ENA = 10;
const int IN1 = 7;
const int IN2 = 4;
const int IN3 = 8;
const int IN4 = 12;
const int ENB = 9;
LMotorController motorController(ENA, IN1, IN2, ENB, IN3, IN4, motorSpeedFactorLeft, motorSpeedFactorRight);

Encoder left(5, 6);
Encoder right(3, 11);

int count = 0;

void setup() {

  pinMode(13, OUTPUT);
  pinMode(10, OUTPUT);
  pinMode(7, OUTPUT);
  pinMode(4, OUTPUT);
  pinMode(8, OUTPUT);
  pinMode(12, OUTPUT);
  pinMode(9, OUTPUT);
  
  pinMode(3, INPUT);
  pinMode(11, INPUT);
  pinMode(5, INPUT);
  pinMode(6, INPUT);

  for (int i = 0; i < AVERAGE_COUNT; i++) {
    speed_values[i] = 0; // fill the array with 0's
  }


  Serial.begin(115200);
  Wire.begin();
  TWBR = ((F_CPU / 400000L) - 16) / 2; // Set I2C frequency to 400kHz

  i2cData[0] = 7; // Set the sample rate to 1000Hz - 8kHz/(7+1) = 1000Hz
  i2cData[1] = 0x00; // Disable FSYNC and set 260 Hz Acc filtering, 256 Hz Gyro filtering, 8 KHz sampling
  i2cData[2] = 0x00; // Set Gyro Full Scale Range to ±250deg/s
  i2cData[3] = 0x00; // Set Accelerometer Full Scale Range to ±2g
  while (i2cWrite(0x19, i2cData, 4, false)); // Write to all four registers at once
  while (i2cWrite(0x6B, 0x01, true)); // PLL with X axis gyroscope reference and disable sleep mode

  while (i2cRead(0x75, i2cData, 1));
  if (i2cData[0] != 0x68) { // Read "WHO_AM_I" register
    Serial.print(F("Error reading sensor"));
    while (1);
  }

  delay(100); // Wait for sensor to stabilize

  /* Set kalman and gyro starting angle */
  while (i2cRead(0x3B, i2cData, 6));
  accX = (i2cData[0] << 8) | i2cData[1];
  accY = (i2cData[2] << 8) | i2cData[3];
  accZ = (i2cData[4] << 8) | i2cData[5];

#ifdef RESTRICT_PITCH // Eq. 25 and 26
  double roll  = atan2(accY, accZ) * RAD_TO_DEG;
  double pitch = atan(-accX / sqrt(accY * accY + accZ * accZ)) * RAD_TO_DEG;
#else // Eq. 28 and 29
  double roll  = atan(accY / sqrt(accX * accX + accZ * accZ)) * RAD_TO_DEG;
  double pitch = atan2(-accX, accZ) * RAD_TO_DEG;
#endif

  kalmanX.setAngle(roll); // Set starting angle
  kalmanY.setAngle(pitch);
  gyroXangle = roll;
  gyroYangle = pitch;
  compAngleX = roll;
  compAngleY = pitch;

  timer = micros();

  // turn the PIDs on
  anglePID.SetMode(AUTOMATIC);
  anglePID.SetSampleTime(10);
  anglePID.SetOutputLimits(-100, 100);
  anglePID.SetTunings(25, 10, 0);

  speedPID.SetMode(AUTOMATIC);
  speedPID.SetSampleTime(10);
  speedPID.SetOutputLimits(-300, 300); // -3 and +3 degrees, respectively
  speedPID.SetTunings(25, 50, 0);

}

long r_wheel, r_wheel_velocity, r_last_wheel;
long l_wheel, l_wheel_velocity, l_last_wheel;

void loop(){

  while (i2cRead(0x3B, i2cData, 14));
  accX = ((i2cData[0] << 8) | i2cData[1]);
  accY = ((i2cData[2] << 8) | i2cData[3]);
  accZ = ((i2cData[4] << 8) | i2cData[5]);
  gyroX = (i2cData[8] << 8) | i2cData[9];
  gyroY = (i2cData[10] << 8) | i2cData[11];
  gyroZ = (i2cData[12] << 8) | i2cData[13];

  double dt = (double)(micros() - timer) / 1000000; // Calculate delta time
  timer = micros();

  // Source: http://www.freescale.com/files/sensors/doc/app_note/AN3461.pdf eq. 25 and eq. 26
  // atan2 outputs the value of -π to π (radians) - see http://en.wikipedia.org/wiki/Atan2
  // It is then converted from radians to degrees
#ifdef RESTRICT_PITCH // Eq. 25 and 26
  double roll  = atan2(accY, accZ) * RAD_TO_DEG;
  double pitch = atan(-accX / sqrt(accY * accY + accZ * accZ)) * RAD_TO_DEG;
#else // Eq. 28 and 29
  double roll  = atan(accY / sqrt(accX * accX + accZ * accZ)) * RAD_TO_DEG;
  double pitch = atan2(-accX, accZ) * RAD_TO_DEG;
#endif

  double gyroXrate = gyroX / 131.0; // Convert to deg/s
  double gyroYrate = gyroY / 131.0; // Convert to deg/s

#ifdef RESTRICT_PITCH
  // This fixes the transition problem when the accelerometer angle jumps between -180 and 180 degrees
  if ((roll < -90 && kalAngleX > 90) || (roll > 90 && kalAngleX < -90)) {
    kalmanX.setAngle(roll);
    compAngleX = roll;
    kalAngleX = roll;
    gyroXangle = roll;
  } else
    kalAngleX = kalmanX.getAngle(roll, gyroXrate, dt); // Calculate the angle using a Kalman filter

  if (abs(kalAngleX) > 90)
    gyroYrate = -gyroYrate; // Invert rate, so it fits the restriced accelerometer reading
  kalAngleY = kalmanY.getAngle(pitch, gyroYrate, dt);

#else
  // This fixes the transition problem when the accelerometer angle jumps between -180 and 180 degrees
  if ((pitch < -90 && kalAngleY > 90) || (pitch > 90 && kalAngleY < -90)) {
    kalmanY.setAngle(pitch);
    compAngleY = pitch;
    kalAngleY = pitch;
    gyroYangle = pitch;
  } else
    kalAngleY = kalmanY.getAngle(pitch, gyroYrate, dt); // Calculate the angle using a Kalman filter

  if (abs(kalAngleY) > 90)
    gyroXrate = -gyroXrate; // Invert rate, so it fits the restriced accelerometer reading
  kalAngleX = kalmanX.getAngle(roll, gyroXrate, dt); // Calculate the angle using a Kalman filter
#endif

  gyroXangle += gyroXrate * dt; // Calculate gyro angle without any filter
  gyroYangle += gyroYrate * dt;
  //gyroXangle += kalmanX.getRate() * dt; // Calculate gyro angle using the unbiased rate
  //gyroYangle += kalmanY.getRate() * dt;

  compAngleX = 0.93 * (compAngleX + gyroXrate * dt) + 0.07 * roll; // Calculate the angle using a Complimentary filter
  compAngleY = 0.93 * (compAngleY + gyroYrate * dt) + 0.07 * pitch;

  // Reset the gyro angle when it has drifted too much
  if (gyroXangle < -180 || gyroXangle > 180)
    gyroXangle = kalAngleX;
  if (gyroYangle < -180 || gyroYangle > 180)
    gyroYangle = kalAngleY;


  // read knobs for angle pid
  double knob0 = analogRead(0);
  double knob1 = analogRead(1);
  double knob2 = analogRead(2);
  double akp = map(knob0, 0, 1023, 0, 30);
  double aki = map(knob1, 0, 1023, 0, 100);
  double akd = knob2/682;

  // read knobs for speed pid
  //double knob2 = analogRead(2);
  double knob3 = 200;
  double skp = 0;
  double ski = 0;

 //best tunings till now: 5.3 45 0.3
 anglePID.SetTunings(5.6, 48, 0.33);
 
 speedPID.SetTunings(0, 0, 0);

  // calculate speed
  l_wheel = left.read();
  r_wheel = right.read();

  l_wheel_velocity = l_wheel - l_last_wheel;
  l_last_wheel = l_wheel;
  r_wheel_velocity = r_wheel - r_last_wheel;
  r_last_wheel = r_wheel;

  int speed = ((l_wheel_velocity + r_wheel_velocity));

  // let's make an average speed for the last N smaples
  int out = 0;
  speed_values[filter_pos] = speed;
  filter_pos = (filter_pos + 1) % AVERAGE_COUNT;
  for (int i = 0; i < AVERAGE_COUNT; i++) {
    out += speed_values[i];
  }
  speedInput = (out / AVERAGE_COUNT);

  // calculate angle setpoint
  speedPID.Compute();
  //angleSetpoint = speedOutput / 100;
  angleSetpoint = -1.3;

 
  /*
    // panic!
    if(abs(angle) >= 20) {
    stop_robot(5000);
    }
  */

  angleInput = kalAngleY;
  anglePID.Compute();

  float go = angleOutput;

  if (go > 0) {
    int speed = map(go, 0, 100, 10, 255);
    motorController.move(speed);
  } else {
    int speed = abs(go);
    speed = map(speed, 0, 100, 10, 255);
    motorController.move(-speed);
  }

  //if(0 == count % 10) {
  Serial.print(akp);
  Serial.print("\t");
  Serial.print(aki);
  Serial.print("\t");
  Serial.print(akd);
  Serial.print("\t");
  /*
  Serial.print(skp);
  Serial.print("\t");
  Serial.print(ski);
  Serial.print("\t");
  */
  Serial.print(angleInput);
  Serial.print("\t");
  Serial.print(angleOutput);
  Serial.print("\t");
  Serial.print(angleSetpoint);
  Serial.print("\t");
  Serial.print(speedInput);
  Serial.print("\t");
  Serial.println(speed);

  //}
  count++;
}

/*
void stop_robot(int duration) {
  motorOff(0);
  motorOff(1);
  delay(duration);
}

void motorOff(int motor) {
  // Initialize braked
  for (int i = 0; i < 2; i++) {
    digitalWrite(inApin[i], LOW);
    digitalWrite(inBpin[i], LOW);
  }
  analogWrite(pwmpin[motor], 0);


void motorGo(uint8_t motor, uint8_t direct, uint8_t pwm) {
  if (motor <= 1) {
    if (direct <= 4) {

      // Set inA[motor]
      if (direct <= 1)
        digitalWrite(inApin[motor], HIGH);
      else
        digitalWrite(inApin[motor], LOW);

      // Set inB[motor]
      if ((direct == 0) || (direct == 2))
        digitalWrite(inBpin[motor], HIGH);
      else
        digitalWrite(inBpin[motor], LOW);

      analogWrite(pwmpin[motor], pwm);

    }
  }
}
}
*/

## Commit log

2017-11-18 Fixing CAD and adding outer PID
    [1_5V_holder4AA.x_t, Arduino.SLDPRT, BATTERY_HOLDER.stp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]
2017-11-20 encoder added
2017-11-27 Finished CAD
    [3D VIEW - Turnigy Batterie Nanotech 1800mAh 2S.IGS, Assem1.SLDASM, Assem2.SLDASM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]
2017-12-05 Added Presentation
    [Bill of Material.xlsx, fritzing connection drawing.fzz]
2017-12-06 Finished Prototype
2017-12-06 File Management
    [1000rpm_12v_25mm_ebay_motor.SLDPRT, 3D VIEW - Turnigy Batterie Nanotech 1800mAh 2S.IGS, Arduino.SLDPRT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]
